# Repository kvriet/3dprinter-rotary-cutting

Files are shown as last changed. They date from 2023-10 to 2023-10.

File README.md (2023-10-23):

# 3D Printer Rotary Cutting Add-On

A 3D printer add-on to enable rotary cutting (vinyl/tape cutting) for PCB creation or otherwise.
CC BY-NC

## Table of contents

1. [The Project](#project)
2. [Materials](#materials)
3. [Assembly](#assembly)
4. [Creating Circuits](#circuit_creation)
   1. [KiCad](#kicad)
   2. [From KiCad to gcode](gcode_creation)
5. [Cutting Circuits](#circuit_cutting)
6. [Examples](#examples)

## The project 

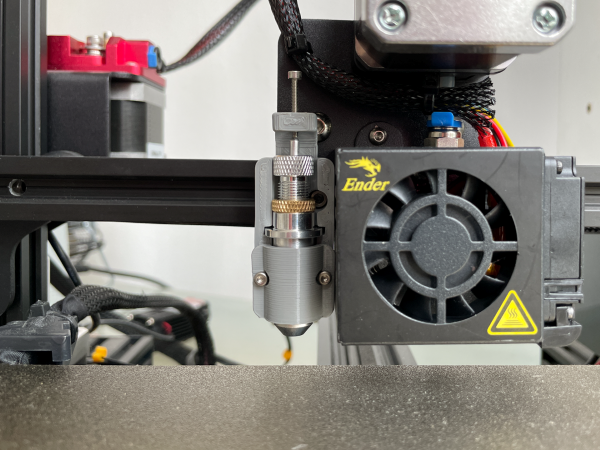
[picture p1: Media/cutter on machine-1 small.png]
Rotary cutter mounted onto 3D-printer

Rotary cutter in action

This project adds rotary cutting capabilities to an existing Ender 3 Pro configuration, but can be attached to other printers too. This add-on will not interfere with the end stops on the Ender and can be left on while printing normally (but maybe retract the knife while printing). This project includes a detailed, step-by-step manual on how to create and cut copper tape for PCB fabrication using sheets of acrylic.

## How to make the rotary cutter holder 

The rotary cutter used here is the Roland Cricut cutting plotter: https://www.aliexpress.com/item/32768955648.html

The holder for the cutter can be 3D printed in PLA without using supports. A layer thickness of 0.2 or 0.3mm will work.

In terms of hardware, you will also need:
- 3x M2x15 bolt for the top to tune how far the knife comes out of the holder, and for the front clamp
- 2x M2 nut for use with the clamp bolts
- 1x M3x8 to secure the vinyl cutter to the Ender

## Printed rotary cutter assembly 

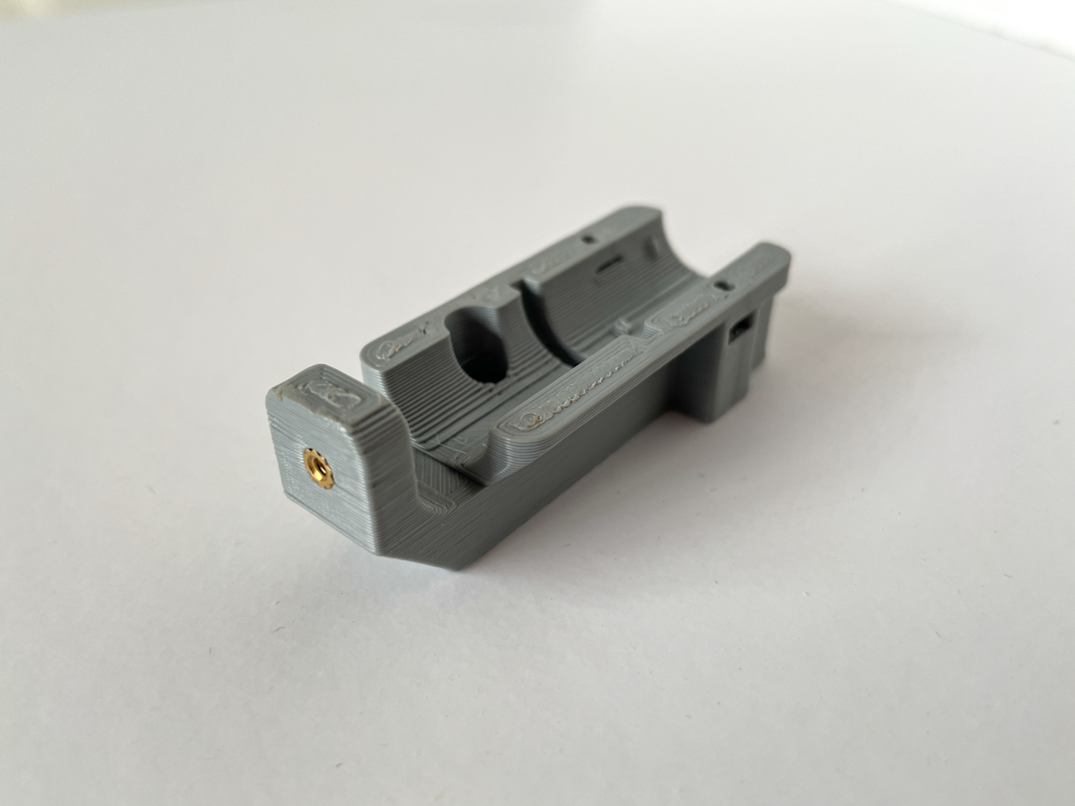
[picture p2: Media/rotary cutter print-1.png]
Print 1


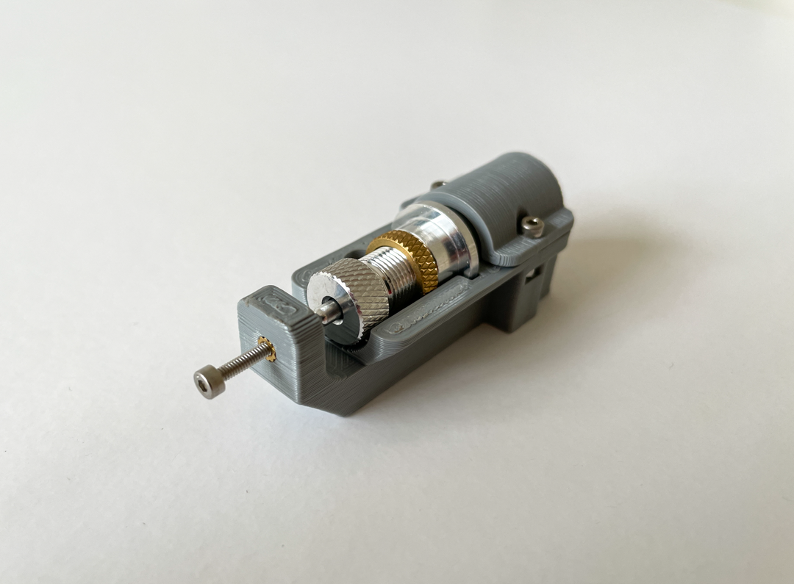
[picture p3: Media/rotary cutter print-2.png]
Print 2


Print 3

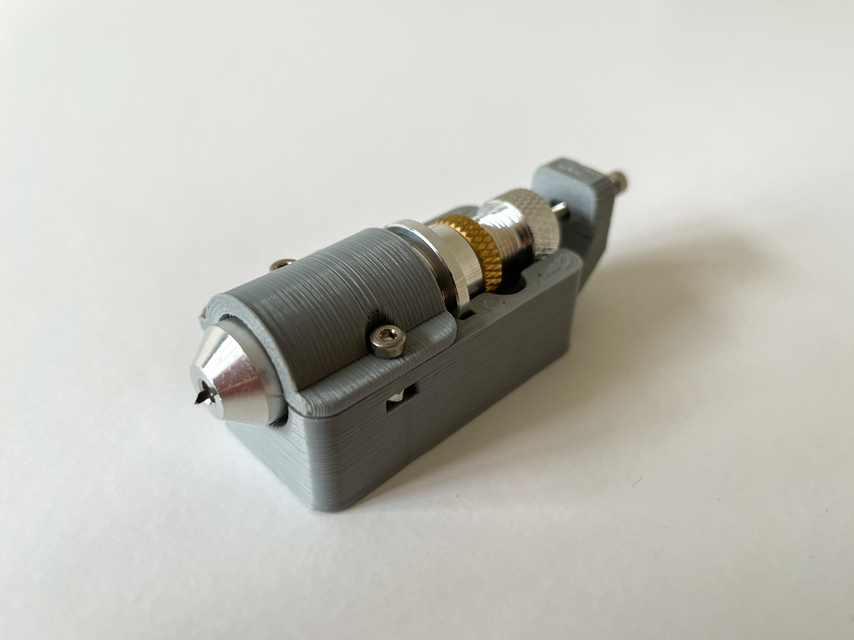
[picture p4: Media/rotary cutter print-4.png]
Print 4


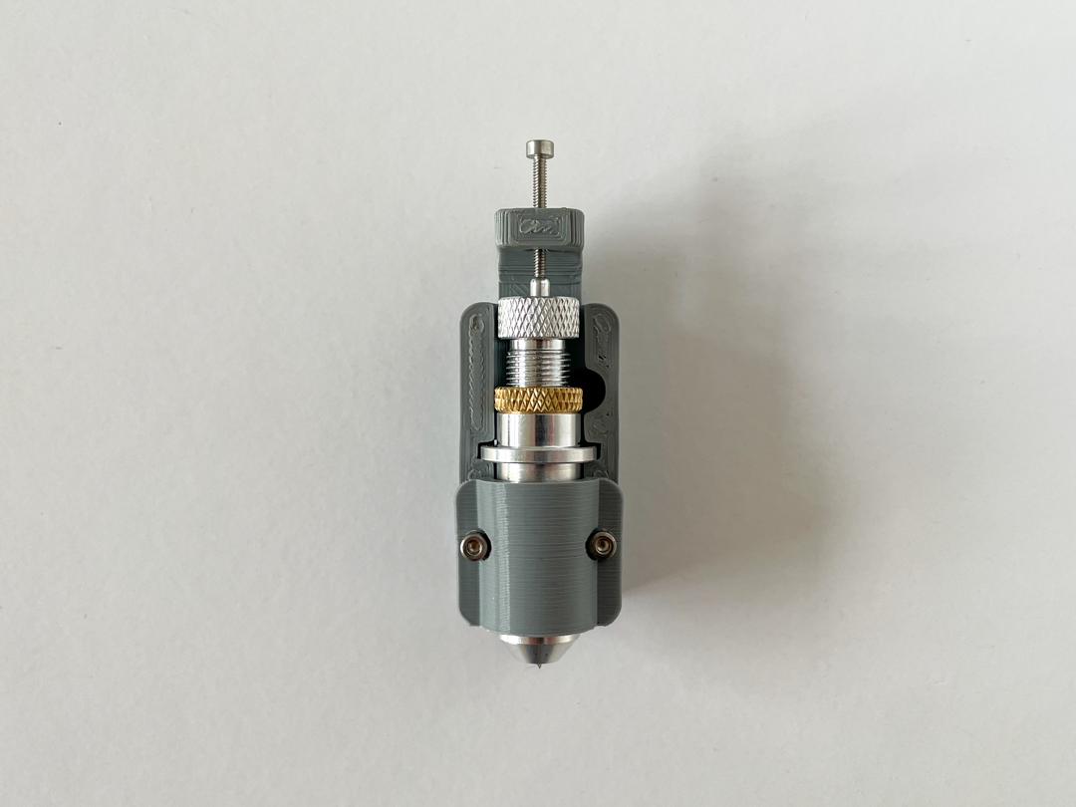
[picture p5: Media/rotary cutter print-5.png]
Print 5


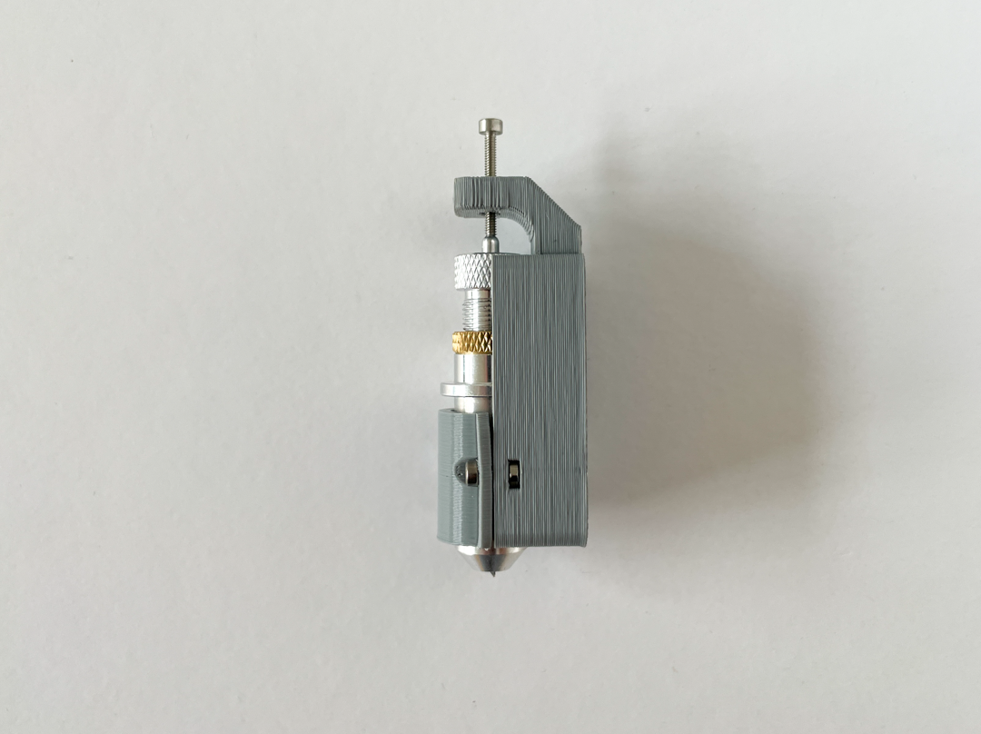
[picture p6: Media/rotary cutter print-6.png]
Print 6


## Creating circuits 

### KiCad 

I design my circuits in KiCad (version 6.0), creating a schematic and then a footprint in the PCB Editor environment. Important for rotary cutting is to minimise the number of sharp corners that the knife has to follow. To create smooth lines, I use the 'fillet tracks' option in KiCad 6.0 with a 3mm fillet radius, but adjust to your own taste. To make tracks smoothly flow into pads, the teardrop plugin can be used, although I have not tried this. I adjust the width of my tracks depending on whether I'm cutting a sticker or tape already applied to acrylic. For stickers, I use 2mm wide tracks as this prevents them from tearing accidentally, or curling up too much on a sticker sheet. For copper tape already applied to the acrylic, the tracks can be 1mm or 0.5mm wide.

### From KiCad to gcode 

Once the KiCad PCB is done, export the copper layers you need (usually just F.Cu or B.Cu) to SVG. Open the SVG in Inkscape. Delete pads and holes. Make sure you just have the tracks. Select all and transform Stroke to Path (Ctrl+Alt+C). Use Union (Ctrl++) to make single objects out of each single track. Select all, set the stroke style to 1px and give it a colour (usually black), and set the infill to none. Make sure your tracks are on a layer.

To create the gcode from this SVG, go to Extensions --> Gcodetools --> Orientation points and click 'Apply'. Next select Tools library from Gcodetools and click 'Apply'. Finally, select Path to Gcode. Under 'Preferences' set the filename (make sure it ends in .gcode) and set Safe Z height to 5mm. Under 'Options' set Z scale to 1mm and Z offset to 2mm, which will make the knife move 1mm over the bed. Under 'Path to Gcode' click 'Apply'. Your gcode will now be created.

The created gcode will start cutting wherever the nozzle is located when the file is activated on the printer. This can be useful for exact circuit placement. If you want the printer start from the origin, add the following gcode to the header:

;; ========== start of inserted gcode  
G28; Home Z (X and Y also)  
G1 X0 Y0 Z5.0 F15240; Move to start position  
;; ========== end of inserted gcode

Fully retract the knife when starting the gcode, then slowly bring it down to start cutting and find the best knife depth for you. The knife should only cut through the copper, not through the sticker backing. Try first with some test lines. You can also do this by setting the nozzle Z height to 1mm, disabling steppers, lowering the knife by turning the screw, and then slowly moving the extruder or the bed and seeing how good the cuts are.

## Cutting circuits 

For creating the copper traces, two main approaches can be taken:
1. Cutting out the traces on the copper tape sticker: First put masking tape on the area of copper tape you want to cut. Then fix the copper tape on the print bed with some clamps or tape. Then the traces can be cut out on the sticker. However, features need to be big and round, otherwise the sticker will curl up and come loose from the sticker. The copper traces can then be transferred from the sticker to the sheet of acrylic using some more masking tape. Once the traces have been transferred, the masking tape needs to be removed.
2. Cutting out the traces on copper already taped to acrylic: First transfer the copper tape to the sheet of acylic. Then fix the acrylic to the print bed using some clamps or tape. Then cut out the traces. Take the acrylic from the printer and remove the copper tape that is not part of the traces. Features can be very small and angular, as the copper tape is already firmly attached to the acrylic and will not start curling.

## Some example circuits cut with this setup 

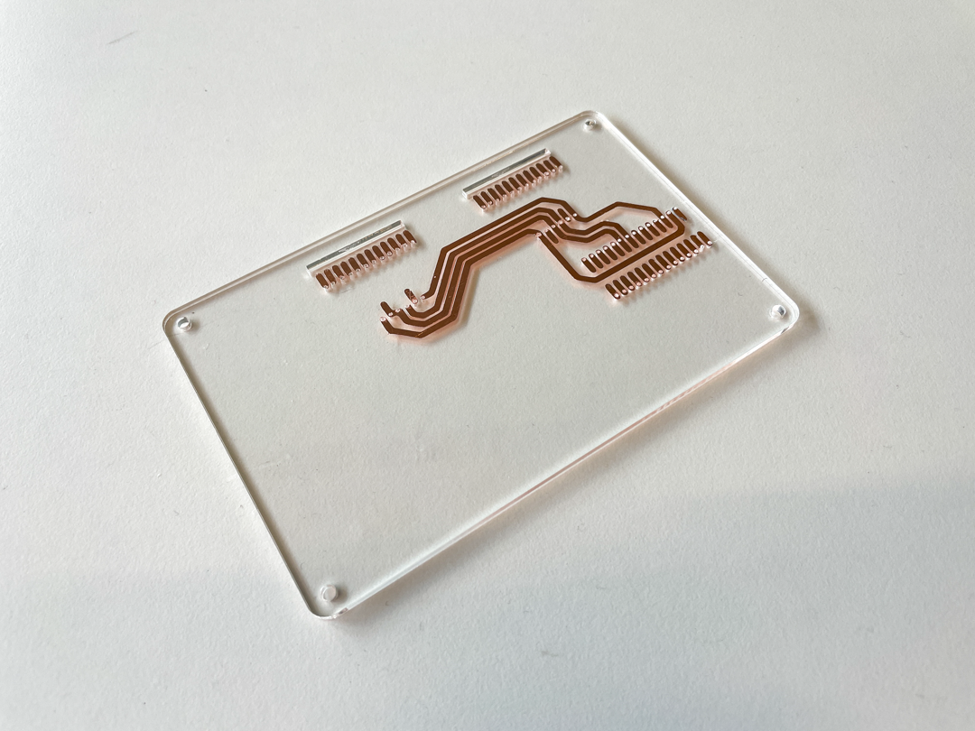
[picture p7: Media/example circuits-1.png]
Example circuit 1


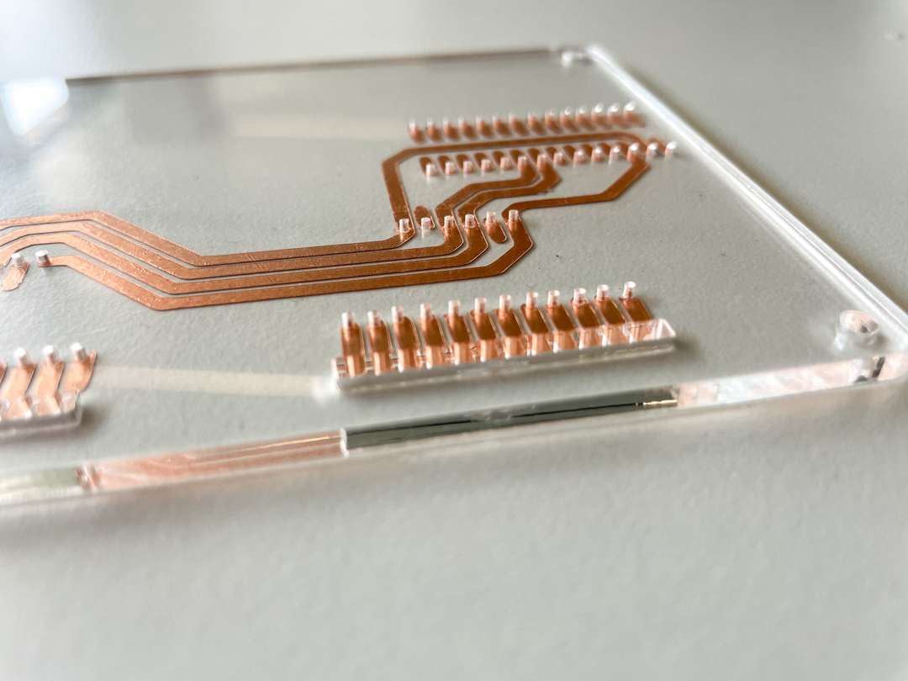
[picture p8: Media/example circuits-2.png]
Example circuit 2


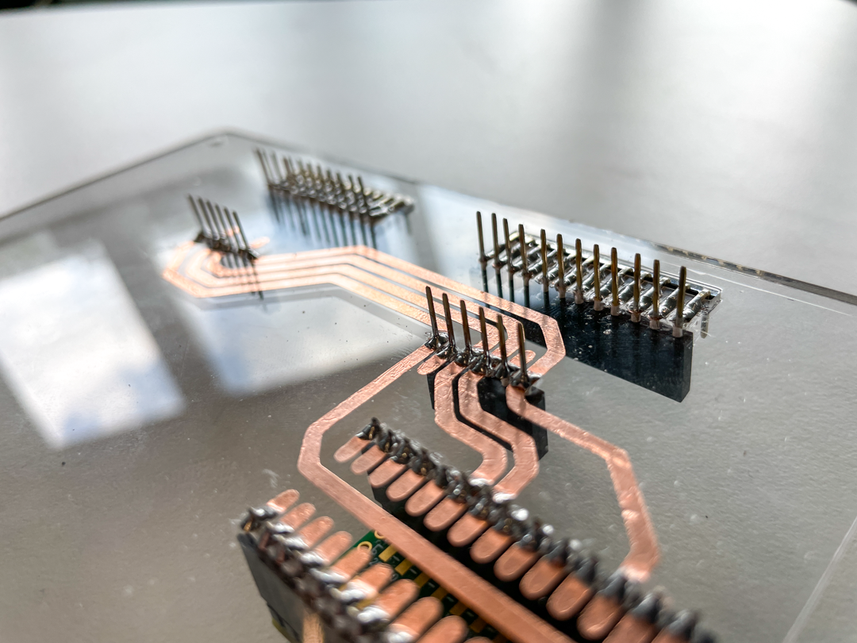
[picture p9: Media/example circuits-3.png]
Example circuit 3


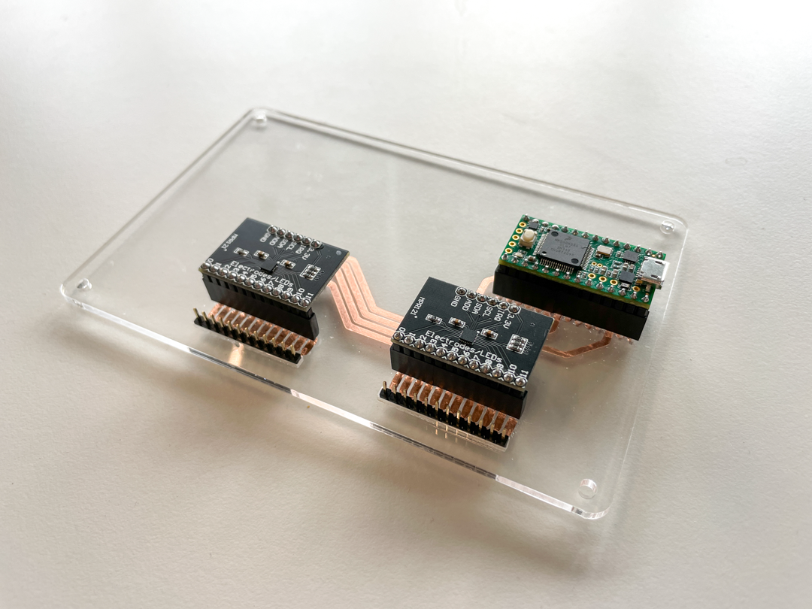
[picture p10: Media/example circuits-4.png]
Example circuit 4


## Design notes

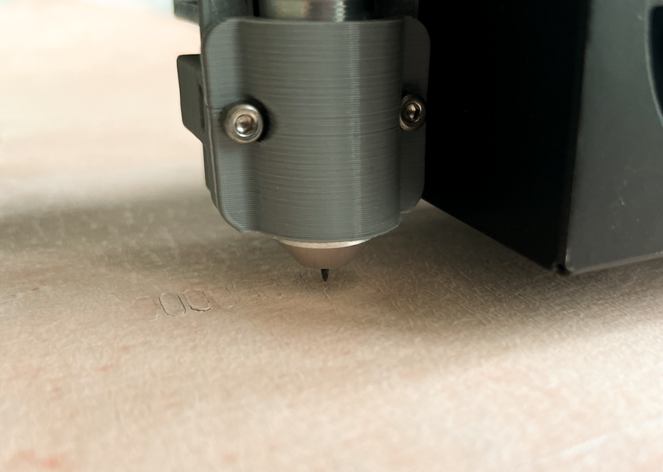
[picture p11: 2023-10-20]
Media/cutting in action-1.png

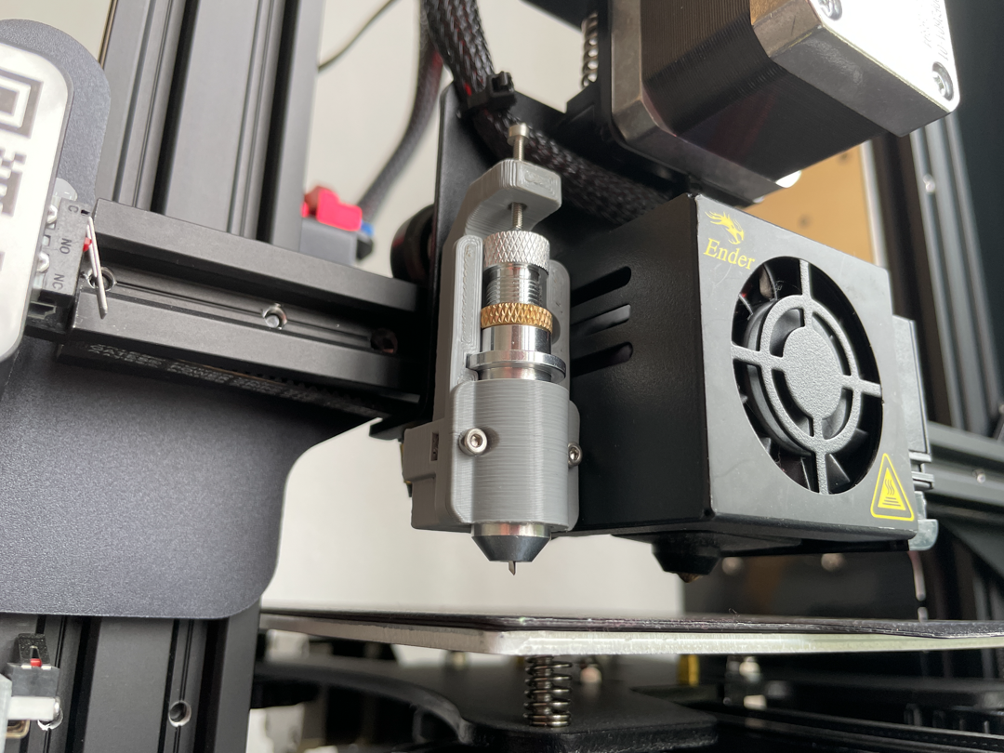
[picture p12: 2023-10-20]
Media/cutter on machine-2.png

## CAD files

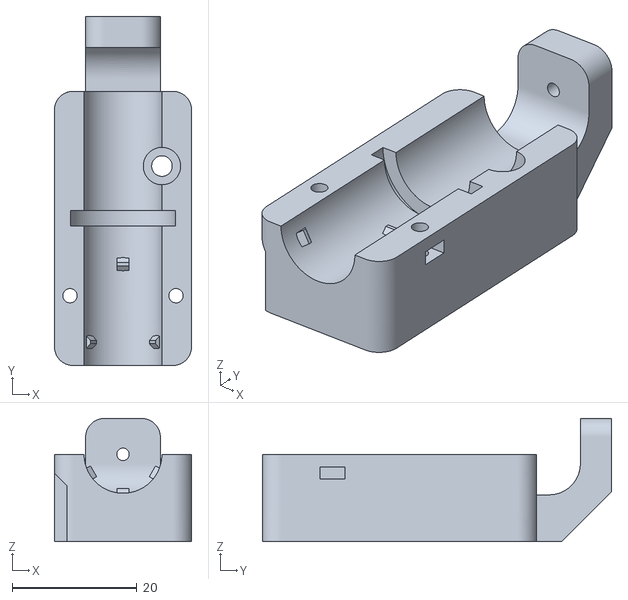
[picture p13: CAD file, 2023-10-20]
Print files/knife holder v3 no insert.stl
22.0 x 56.0 x 19.8

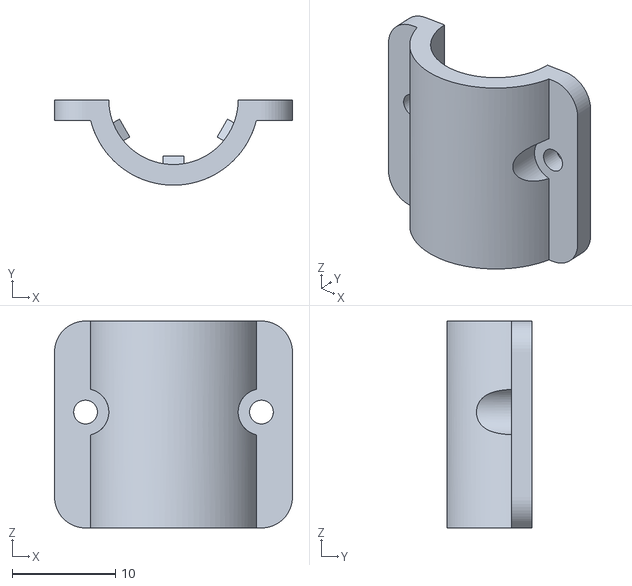
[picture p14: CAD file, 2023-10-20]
Print files/clamp v2.stl
23.0 x 8.25 x 20.0

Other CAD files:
Print files/knife holder v4 threaded insert M2.stl

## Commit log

2023-10-20 added print files
    [clamp v2.stl, knife holder v3 no insert.stl, knife holder v4 threaded insert M2.stl]
2023-10-20 Updated knife holder stls
    [knife holder v3 no insert.stl, knife holder v4 threaded insert M2.stl]
